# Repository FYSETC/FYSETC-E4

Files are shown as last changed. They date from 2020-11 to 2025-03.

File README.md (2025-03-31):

## Product Introduction

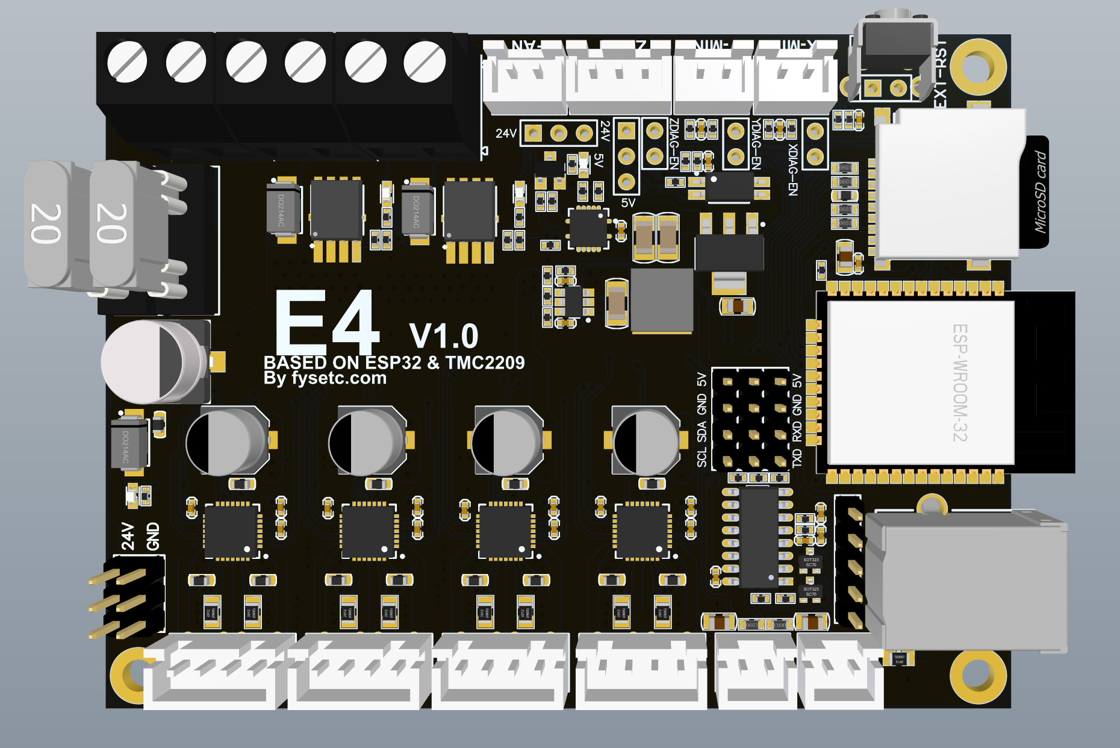
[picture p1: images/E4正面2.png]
E4正面2


The E4 board is a minimal 3D printer control board based on the ESP32 microcontroller from ESPRESSIF, with built-in Wi-Fi and Bluetooth. The controller speed is up to 240MHz, 16M flash.

## Features

- Compact size: 90mm x 67mm
- Native Wi-Fi support
- 12V to 24V input power supply, 3 power outputs and 3 5V outputs
- 4 * **TMC2209** stepper drives: X, Y, Z and E axis
- Onboard TF card socket
- CH340 for high speed USB serial connection 
- X, Y, and Z min endstops; also supports sensorless homing
- Allows the use of a Z-axis probe, such as an inductive sensor, running on the input supply voltage (12V to 24V) or 5V
- A controllable fan, you can choose the power supply voltage (12/24V) or 5V voltage for it
- Xh2.54 connector, firm and easy to plug
- PCB：
  - Black matte ink,lead-free tin spray process
  - High quality, High temperature FR4-TG130 PCB

## Why do you need this board?

If you want to be able to control your 3D printer via a web browser without having to buy extra components like a Raspberry Pi for Octoprint, this board is for you. If you run a printing farm and want to be able to start prints remotely via Wi-Fi, this board is for you. 

### Native Wi-Fi support

FYSETC E4 is based on the ESP32 microcontroller, so the E4 supports 802.11 b/g/n protocols, and a custom fork of Marlin firmware can be used on the board to allow the board to be controlled via a web browser.

This removes the need for the traditional LCD controllers that most other boards use. There is also no need to connect a Raspberry Pi in order to control the printer via a web interface. The web interface is the popular ESP3D webUI, which runs natively on the custom Marlin fork. The printer can then be controlled via any web browser, be it a PC, smart phone, or tablet.

For example, you can slice your 3D model using a slicing software on your PC, then use your PC's web browser to connect to the printer, send the sliced GCODE file to the printer via Wi-Fi. Then, using the same web browser, you can tell the printer to start printing away.

### Trinamic stepper drivers

FYSETC E4 use the latest ,best stepper drvier : TMC2209.

1. Ultra quiet
2. Good heat dissipation
3. Max current up to 2A
4. Large heat sink,good heat dissipation
5. Support sensorless-homing function.

### High voltage for probes

One common problem when using inductive or capactive probes is the voltage which they are powered at. These probes are usually connected to the Z endstop, which is powered directly by the microcontroller. This means 5V or 3.3V, but these probes are not designed for such low voltages. Instead, they are usually designed for operation at 6V or more. Using a lower voltage to operate such probes reduces their detection distance, and therefore their effectiveness.

The FYSETC E4 has a dedicated connector for such a Z probe which uses the voltage of the power supply to power the probe. If you are using 12V for the power supply, the probe will be running on 12V, and vice versa for when using a 24V power supply. This allows the probe to operate within its specifications, delivering optimal detection distances.

### Onboard or External Antenna

There are two versions of the E4 board. One is that the antenna of the WiFi module is onboard. And the other is a WiFi module with an external antenna. This option give you the choice  that if you want to install board in a closed box, the external antenna can avoid the problem of WIFI signal weakening in a confined space.

| Onboard Antenna | External Antenna |
| --- | --- |
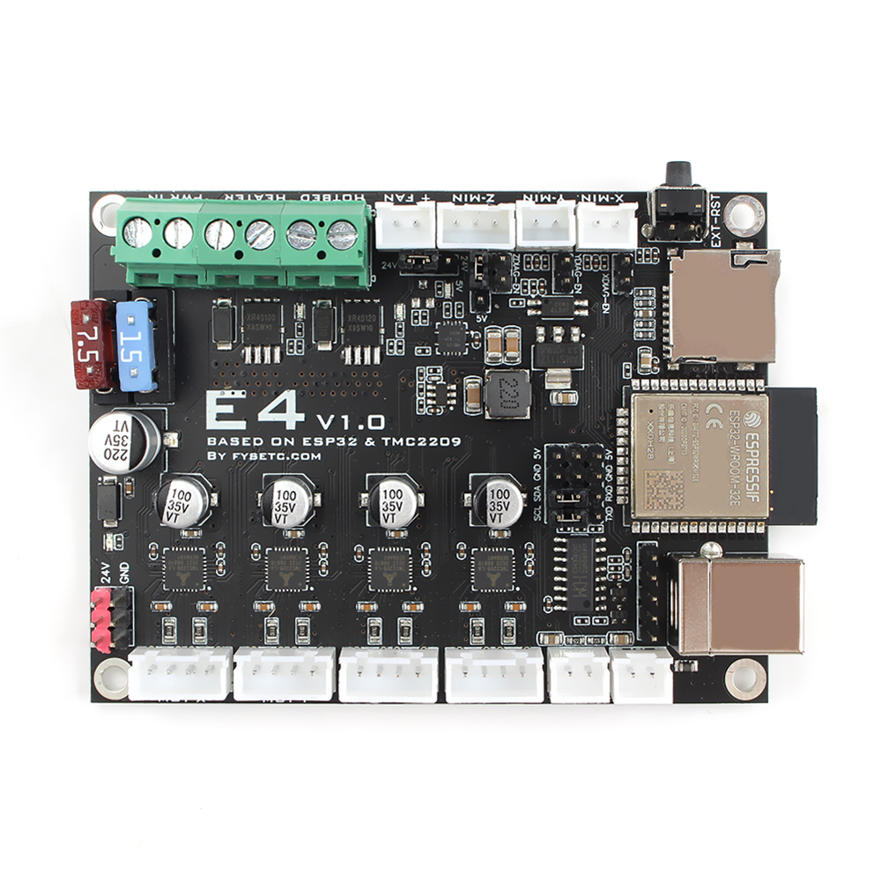
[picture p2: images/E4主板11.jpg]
E4主板11
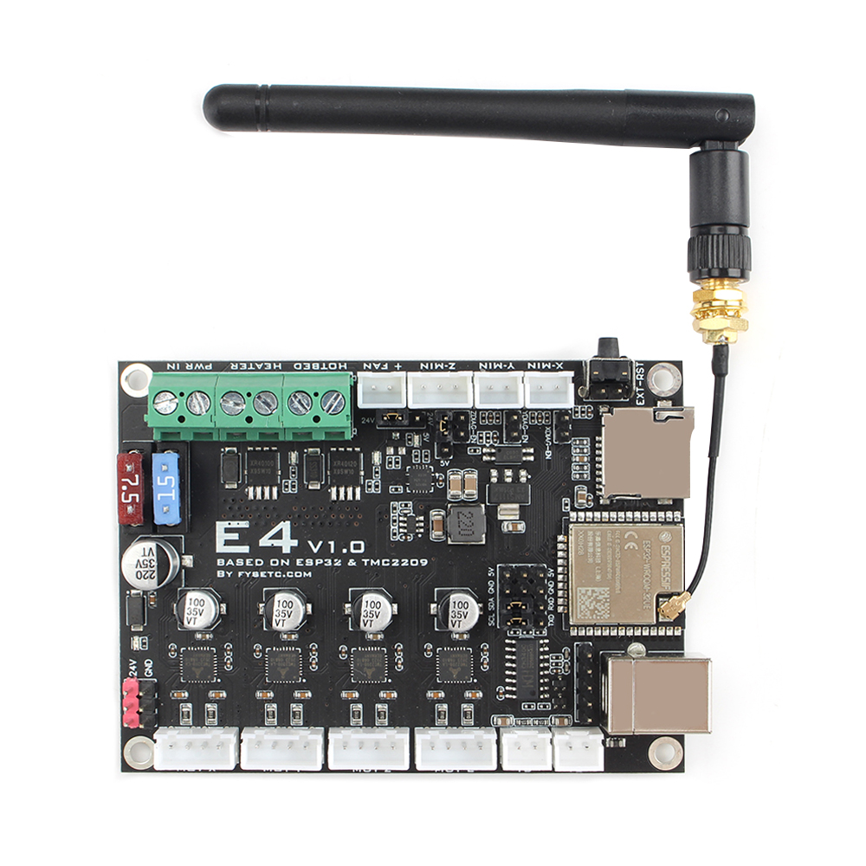
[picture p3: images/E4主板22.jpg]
E4主板22
|  |  |

## Hardware Reasources

E4正面

| Board Name | E4 |
| --- | --- |
| Latest Version | V1.0 |
| Extruders | 1 |
| Hotbed | 1 |
| Controlled Fans  | 1 |
| Heaters | 1 |
| Endstops | 3 |
| Temp sensor | 2 |
| Serial port chip | CH340 |
| CPU | 240MHz [ESP32-WROOM-32E](https://www.espressif.com/sites/default/files/documentation/esp32-wroom-32e_esp32-wroom-32ue_datasheet_en.pdf), [ESP32-WROOM-32UE](https://www.espressif.com/sites/default/files/documentation/esp32-wroom-32e_esp32-wroom-32ue_datasheet_en.pdf) |
| FLASH Size | 16MB |
| Stepper driver | 4 * TMC2209 |
| Input | Main PWR：12-24V 22.5A Max |
| Output | BED+Heater OUT：15A Max |

## Jumper Introduction

**Fan power jumper**

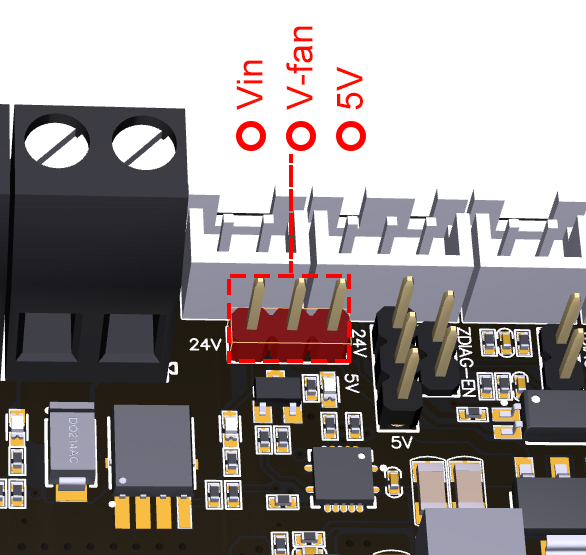
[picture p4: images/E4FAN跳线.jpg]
E4FAN跳线


**Z-Probe power jumper**

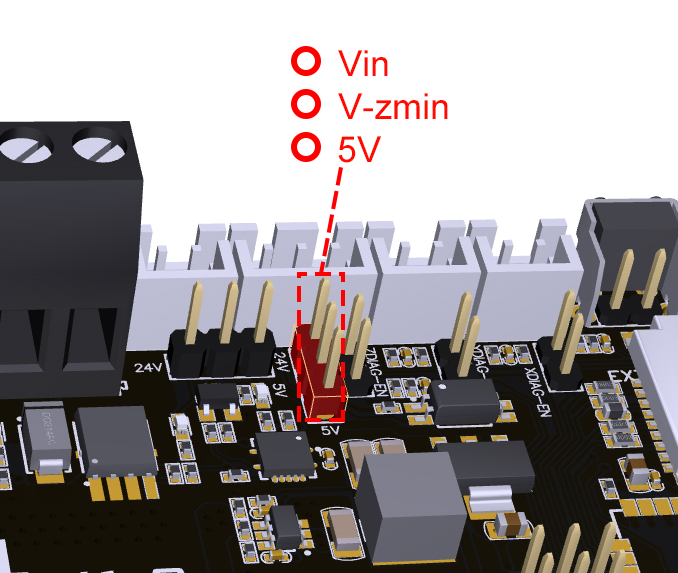
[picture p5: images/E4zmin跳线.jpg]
E4zmin跳线


**Sensorless homing enable jumper**

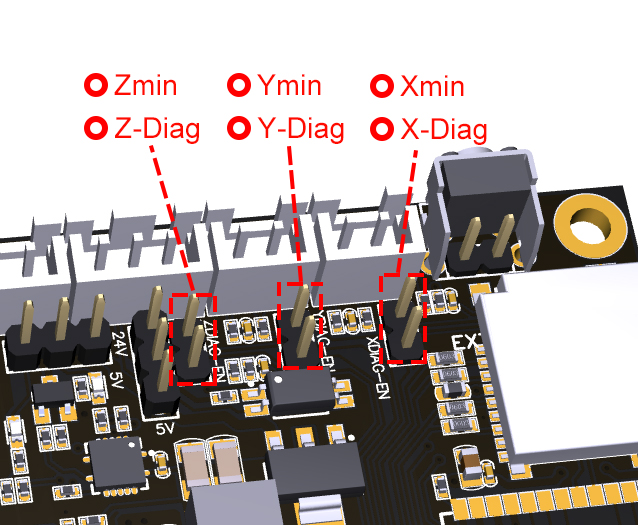
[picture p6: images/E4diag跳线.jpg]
E4diag跳线


**Sensorless homing enable jumper**

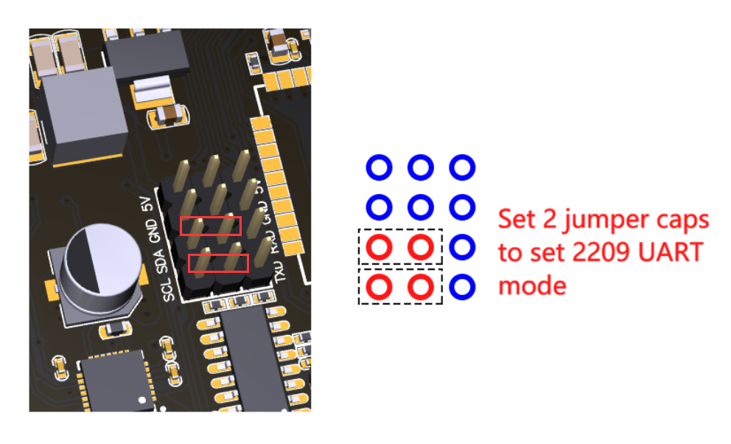
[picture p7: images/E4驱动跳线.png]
E4驱动跳线


## Pin Definition

<table>
   <tr><td>Features</td><td>E4 Pin</td><td>ESP32 Pin</td><td>Pin No.</td><td>Comment</td></tr>
   <tr><td rowspan="3">X-MOTOR(1)</td><td>X-Step</td><td>27</td><td>12</td><td></td></tr>
   <tr><td>X-DIR</td><td>26</td><td>11</td><td></td></tr>
   <tr><td>X-EN</td><td>25</td><td>10</td><td></td></tr>
   <tr><td rowspan="3">Y-MOTOR(2)</td><td>Y-Step</td><td>33</td><td>9</td><td></td></tr>
   <tr><td>Y-DIR</td><td>32</td><td>8</td><td></td></tr>
   <tr><td>Y-EN</td><td>25</td><td>10</td><td></td></tr>
   <tr><td rowspan="3">Z-MOTOR(3)</td><td>Z-Step</td><td>14</td><td>13</td><td></td></tr>
   <tr><td>Z-DIR</td><td>12</td><td>14</td><td></td></tr>
   <tr><td>Z-EN</td><td>25</td><td>10</td><td></td></tr>
   <tr><td rowspan="3">E0-MOTOR(4)</td><td>E0-Step</td><td>16</td><td>27</td><td></td></tr>
   <tr><td>E0-DIR</td><td>17</td><td>28</td><td></td></tr>
   <tr><td>E0-EN</td><td>25</td><td>10</td><td></td></tr>
   <tr><td rowspan="3">SPI </td><td>MOSI</td><td>23</td><td>37</td><td></td></tr>
   <tr><td>MISO</td><td>19</td><td>31</td><td></td></tr>
   <tr><td>SCK</td><td>18</td><td>30</td><td></td></tr>
   <tr><td rowspan="3">End-stops</td><td>X-MIN</td><td>34</td><td>6</td><td>Share with X-DIAG</td></tr>
   <tr><td>Y-MIN</td><td>35</td><td>7</td><td>Share with Y-DIAG</td></tr>
   <tr><td>Z-MIN</td><td>15</td><td>23</td><td>Share with Z-DIAG</td></tr>
   <tr><td rowspan="1">FAN</td><td>FAN0</td><td>13</td><td>16</td><td></td></tr>
   <tr><td rowspan="2">Heating</td><td>E0-Heater</td><td>2</td><td>24</td><td></td></tr>
   <tr><td>Heated-Bed</td><td>4</td><td>26</td><td></td></tr>
   <tr><td rowspan="2">Temperature</td><td>TE0（THERM0）</td><td>36</td><td>4</td><td>A 4.7kOhm 0.1% temperature sensor pull up resistor is used,PT1000 can be connected directly. For PT100, an amplifier board must be used.</td></tr>
   <tr><td>TB</td><td>39</td><td>5</td><td></td></tr>
   <tr><td rowspan="2">MOTOR UART</td><td>TX1</td><td>22</td><td>35</td><td></td></tr>
   <tr><td>RX1</td><td>21</td><td>34</td><td></td></tr>
</table>

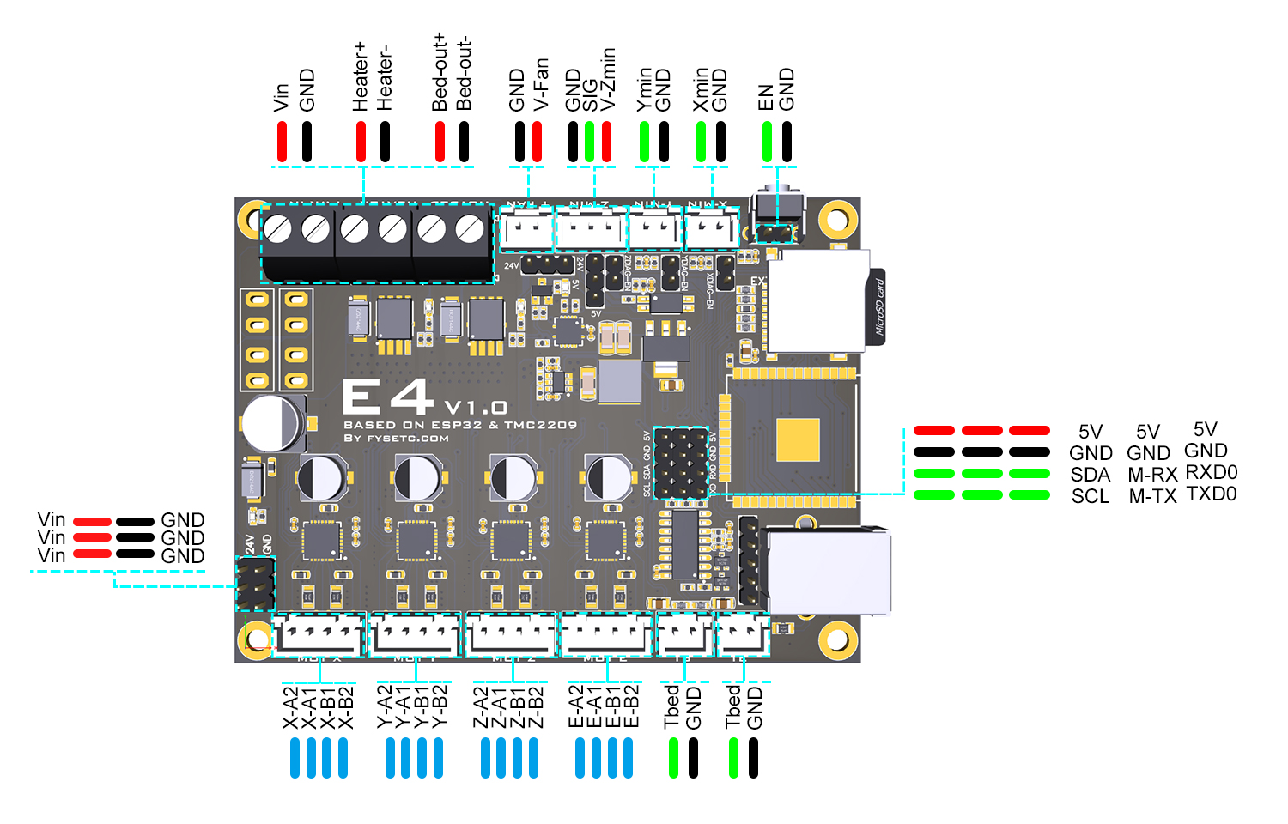
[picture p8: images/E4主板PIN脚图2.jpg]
E4主板PIN脚图2


## Dimensions

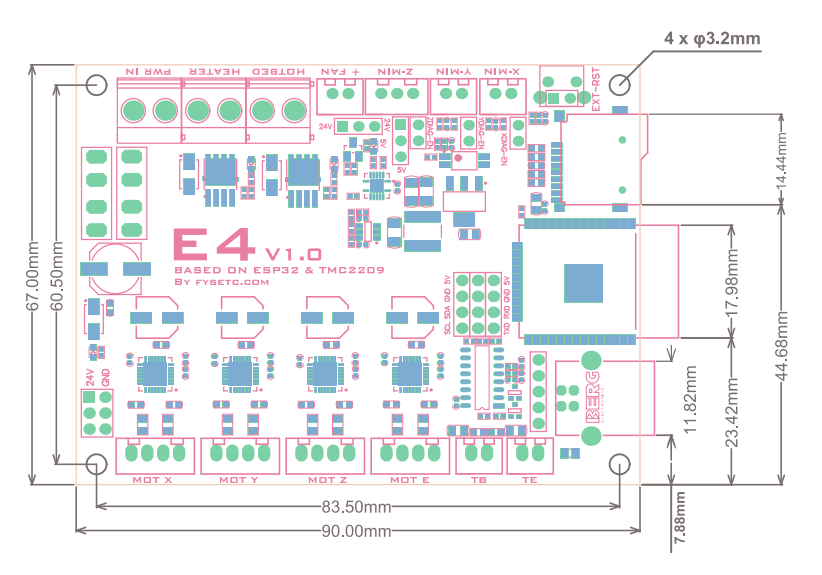
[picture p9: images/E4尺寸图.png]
E4尺寸图


---

- [Schematic and PCB files](https://github.com/FYSETC/FYSETC-E4/tree/main/hardware)

## Firmware

### How to use

The factory firmware comes flashed with the custom fork of Marlin as well as the web interface. You can get it in our [github](https://github.com/FYSETC/FYSETC-E4). Always you need to modify it base on your machine configuration. You can follow our [video](https://youtu.be/Skz7xW8TiHI) or the following steps :

1. Turn on power to the FYSETC E4, and then connect your PC, smart phone, or tablet to the SSID "MARLIN_ESP" (default password is "12345678").
2. Once connected, open a web browser, and go to "[http://192.168.0.1/](http://www.google.com/url?q=http%3A%2F%2F192.168.0.1%2F&sa=D&sntz=1&usg=AFQjCNHmcUXoQvvfhtmwWsGrZOfa2vJB6A)" which will load the ESP3D web interface.
3. Go to the "ESP3D" tab, and enter your WiFi settings (SSID and password).
4. Reset the FYSETC E4. It should now connect to your router.
5. Connect the USB cable to E4 and your PC with 115200 baudrate, and send Serial command "[ESP111]" to get the E4 IP address.
6. Use your web browser and visit the IP address you just get to access the web interface.
7. You can now update the firmware. Download the custom fork from [here](https://github.com/FYSETC/FYSETC-E4/tree/main/firmware), edit Configuration.h and Configuration_adv.h to suit your needs, then compile. In PlatformIO, you can add "upload_port = ip adderrs of your E4" to your platformio.ini file to allow OTA updates. Or, after the firmware has been compiled, use the web interface, go to "ESP3D" tab, and there is an option for firmware update that allows up to upload the firmware.bin file.

### Compile the firmware yourself

If you want to compile the firmware yourself, you need to 

1. Edit the `configuration.h` and `configuration_adv.h` file , please follow the README [here](https://github.com/luc-github/ESP3DLib).

2. Change env in `platformio.ini` to `FYSETC_E4`
   
   ```default_envs = FYSETC_E4```

#### Marlin 2.1.x

Get the code from Marlin github [here](https://github.com/MarlinFirmware/Marlin), and the related configuration [here](https://github.com/luc-github/MarlinConfigurations/tree/bugfix-2.1.x/config/examples/FYSETC/E4).

## Shop

---

- [Taobao](https://item.taobao.com/item.htm?spm=a230r.1.14.22.66cd74cfpASnTX&id=641701271442&ns=1&abbucket=1#detail)
- [Aliexpress](https://www.aliexpress.com/item/1005001703930983.html)

## Tech Support

---

Please submit any technical issue into our [github](https://github.com/FYSETC/FYSETC-E4) or [forum](http://forum.fysetc.com/)

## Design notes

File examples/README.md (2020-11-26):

# Examples

This folder will contains machine examples that E4 board supporting. If you can't find your printer here , it does not mean E4 board does not support it , just because we don't add it at the moment. We strongly encourage you to make PR  for us and here is the [tutorial](https://docs.github.com/en/free-pro-team@latest/github/collaborating-with-issues-and-pull-requests/creating-a-pull-request). Thanks for your support.

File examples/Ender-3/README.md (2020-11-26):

# Ender3

This  setup up guide is for installing FYSETC E4 to Ender3  machine.

## Structure

You need to print two files with your 3D printer first named ```Case.STL``` and ```Cover.STL```. Then uninstall the original Ender 3 case and cover, then install these two printing part to Ender3.  

## Firmware

Replace Marlin with ```configuration.h``` and  ```configuration_adv.h``` beside this README  file. Then compile and upload.

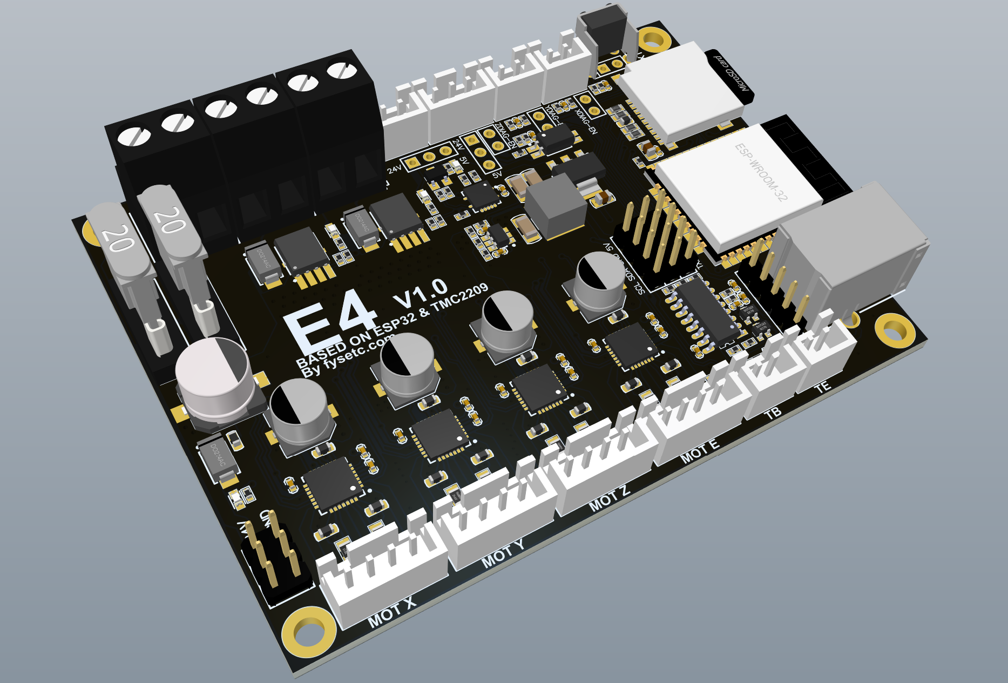
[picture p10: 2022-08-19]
hardware/E4_3Dview.png

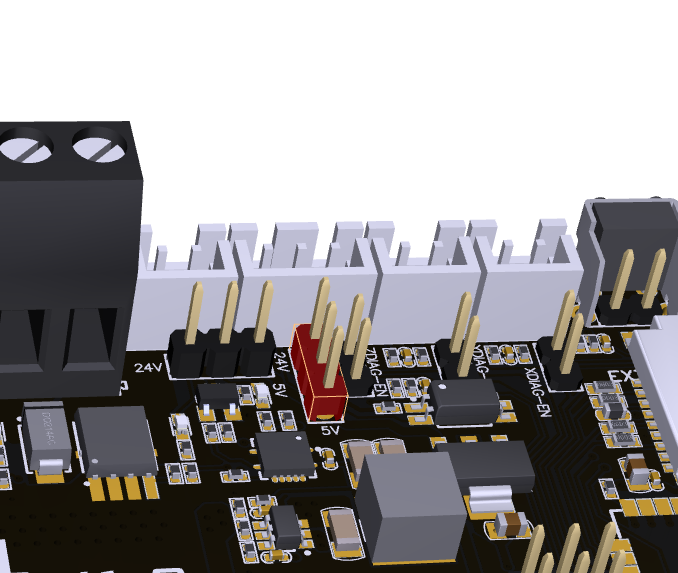
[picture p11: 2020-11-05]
images/E4zmin跳线.png

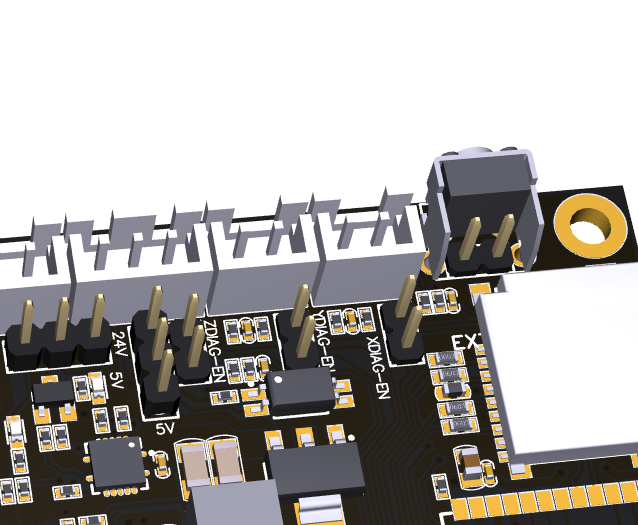
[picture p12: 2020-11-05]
images/E4diag跳线.png

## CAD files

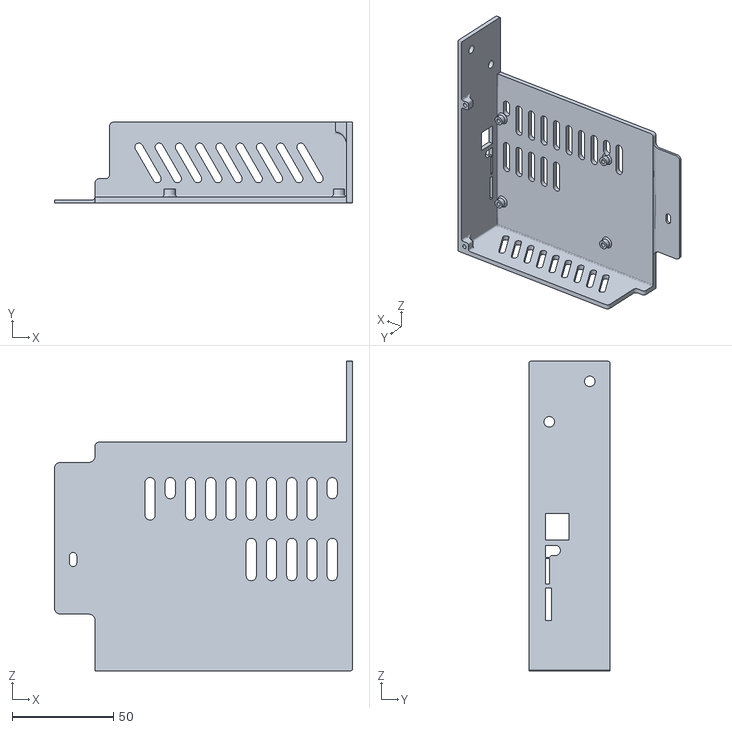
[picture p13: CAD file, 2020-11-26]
examples/Ender-3/Case.STL
147.2 x 40.0 x 153.0

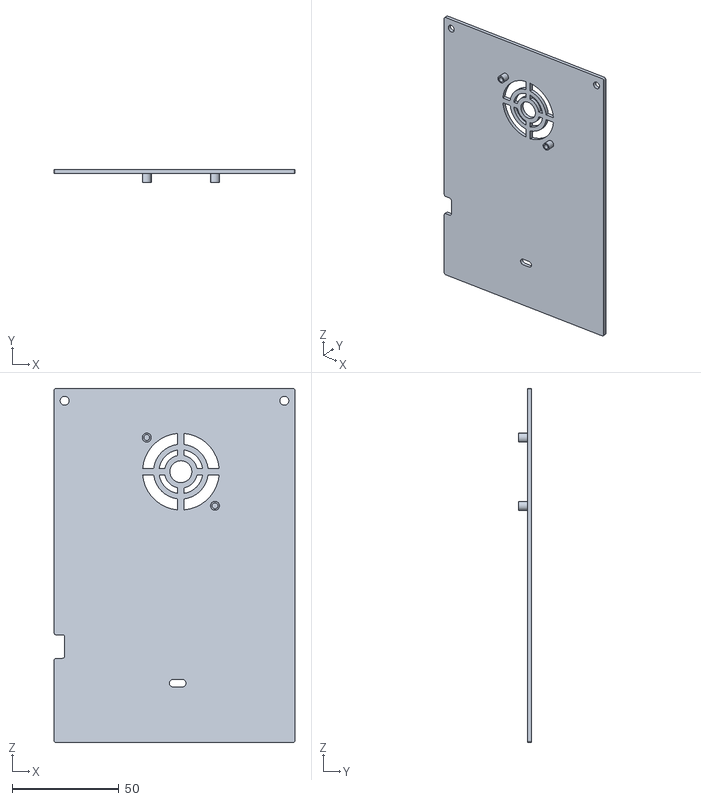
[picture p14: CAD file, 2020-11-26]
examples/Ender-3/Cover.STL
113.0 x 6.20 x 166.0

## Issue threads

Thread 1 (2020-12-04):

FYSETC-E4 Setup Example For a Delta Printer

Loadmaster1, 2020-12-04:
The provided E4 is for a cartesian printer.  Is there a chance of a working example for a Delta type of printer?  I have a Tevo Little Monster that I am trying to use the E4 with.  I keep having issues with the build failing.  Something to do with the Pins.

I will continue to try and resolve the build error, but any input would be much appreciated.

GerogeFu, 2020-12-04:
Sorry , this board only have 3 endstops pin. And there is no enough pin for a servo or bltouch.  But i have a thought , if you don't have a heatbed , maybe you can use the heatbed pin PC9 for bltouch. That means , you need to change pins_FYSETC_E4.h file as below.

Loadmaster1, 2020-12-04:
Geroge,  thank you for your suggestion.  I will give it a go and see if I can figure this out.

Loadmaster1, 2020-12-04:
Geroge, I really like the design and wifii of the E4 board.  Does FYSETC have any plans to build a board like the E4 with added endstops for use with a Delta design?  I believe there is a huge market for such.  It would be worth considering.

GerogeFu, 2020-12-05:
Yes , we are planning now. Hope more and more people like E4 boards. And it is nealy support Grbl_ESP32 firmware now. https://github.com/bdring/Grbl_Esp32

Loadmaster1, 2020-12-05:
That is great news.  You guys did a nice job on the E4.  Yes, I'm sure there will be a lot of interest.

________________________________
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

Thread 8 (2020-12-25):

Fan always on

sdavidozzo, 2020-12-25:
I installed the firmware found here on my ender 3 but the fan is always on.
Sending the M106 S0 command or the M107 command gives me a message:
Ok
ok
but the fan remains on as well as the LED on the board.

GerogeFu, 2021-01-06:
Can you take a pic for me? It is a bit hard to tell from what you describe.

sdavidozzo, 2021-01-13:
[image: E4.jpg]
When I turn on the printer, the fan for cooling the filament turns on as
well as the red LED. When printing begins, the fan stays on and in this way
the piece does not stick to the plate. It never goes out even when sending
the M106 S0 command

Il giorno mer 6 gen 2021 alle ore 09:16 George Fu <notifications@github.com>
ha scritto:

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

GerogeFu, 2021-01-27:
Are you using stock firmware ? Or you compile the firmware yourself ?

sdavidozzo, 2021-01-27:
I tried both with stock firmware and compiled firmware but can’t solve the problem

Inviato da iPad

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

GerogeFu, 2021-02-02:
Do you have a multimeter? You can measure the vol of mosfet pin1 , if the voltage changes if you send commands(M106) to turn it on then off. Then the mosfet is dead. If the voltage of pin1 not change, that is the firmware or other issue not mosfet.
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

sdavidozzo, 2021-02-02:
The volt of mosfet pin1 change from 0 (M106 S0) to 1,84 volt (M106 S200) . The mosfet is dead?

GerogeFu, 2021-02-03:
Can you measure this pin vol for me ?
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

GerogeFu, 2021-02-04:
No matter how, contact our sales to send you another E4 board for you.

iNDeX999, 2021-08-06:
I had the same problem, Mosfet dead, new board is on it's way.

sdavidozzo, 2021-08-07:
I had to reinstall the original card and am still waiting for the replacement. I have lost all hope of seeing this card working by now.

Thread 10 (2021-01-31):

Config marlin

smashemQuads, 2021-01-31:
Need help custom config marlin. Vs code platform io.
Librays dont install
Bugfix doesnt have e4 board.
Where do i get a working version i can edit please

GerogeFu, 2021-02-01:
The lastest  bugfix2.0 has E4
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

smashemQuads, 2021-02-20:
Fixed, Issue is with VS code not getting libaries.

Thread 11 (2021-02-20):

PIN Numbers please

smashemQuads, 2021-02-20:
Can I get the Pin numbers for RXD0 and TXD0
Are they allocated to anything?
Thanks

Tigger777, 2021-04-21:
The schematic is in this repo, those pins are used for USB Serial comms.

iNDeX999, 2021-08-06:
The ESP32 has 3 uart:

<html>
<body>
<!--StartFragment-->

UART0 | GPIO3 | GPIO1 | N/A | N/A
-- | -- | -- | -- | --
UART1 | GPIO9 | GPIO10 | GPIO6 | GPIO11
UART2 | GPIO16 | GPIO17 | GPIO8 | GPIO7

<!--EndFragment-->
</body>
</html>

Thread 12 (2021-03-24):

Servo Usage, which pin is accessible?

theomega, 2021-03-24:
I want to use a servo instead of the Z-Axis Stepper motor. The servo would be PWM controlled which is something the ESP32 firmware can support on every GPIO pin.

Is there any GPIO pin from the ESP32 accessible on the board that can be used for this?

Tigger777, 2021-04-21:
I used GPIO0 for a Z-probe ABL servo. You need to solder a wire to the ESP32 (bottom pin on the RHS). You also need a pull-up to 3v3 else it won't always boot.  I had already installed everything so I just tied to to 5V with a 39k resistor.

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

lols, 2021-06-16:
you can use the z-min plug for servo but you need to see the board pcb
-remove the opto isolator + filter cap + 3.3v pull up resistor(red box)
-bridge the opto isolator pin(green line)
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

car-par, 2024-10-20:
Hi, I'm new to this and I would like to use a BLTouch on a Fysetc E4 but idk where to connect the PWM cable... and I didn't really understand what you all said in the comments above... Please could someone help me?

Tigger777, 2024-10-21:
> Hi, I'm new to this and I would like to use a BLTouch on a Fysetc E4 but idk where to connect the PWM cable... and I didn't really understand what you all said in the comments above... Please could someone help me?

Look above at my screenshot, the orange arrow is pointing to GPIO0, thats where to connect the PWM signal.
Can you build the Marlin code? This has been quite an undertaking for me every time there have been updates.

car-par, 2024-10-28:
Hi, sorry if I'm replying after a week, I didn't see you had replied. Ok I understood that I had to connect the PWM to GPIO0 but as for the rest it's not clear to me how to proceed. And yes I can build the code. Thanks for your reply

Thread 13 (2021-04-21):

Print pauses and leaves blobs

Tigger777, 2021-04-21:
I've experienced some issues which I think are related to web access.  I've not looked how the websockets have been implemented but I trust the people who wrote the code are better programmer than me.

It appears to happen when my PC goes to sleep (iMac) with safari open on the ESP3D page.

I make a point of closing the browser tab every time as a work around, and I've only seen it once leave a blob in a 12 hour print.

I replaced a random layer shifting board in a Ender 3 V2 with this one and I am very pleased with the results.  The vertical walls are so much cleaner/smoother.

Also the machine uses less power now, the PSU fan turns off during a print and the hottest stepper motor is now 38 degC, I couldn't touch them on the stock setup.

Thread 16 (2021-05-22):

How to connect a bltouch without heatbed?

lols, 2021-05-22:
How can I connect all the pins to a bltouch?
I can solder/cut trace etc just don't know which pin to use and config

KittyDotNet, 2022-09-16:
change your homing to
```
//#define QUICK_HOME
#define HOME_Y_BEFORE_X
```
to fix the end stop issue

Closed 2021-06-16.

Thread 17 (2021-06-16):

Fix the bottom silkscreen

lols, 2021-06-16:
The bottom silkscreen is different from the top silkscreen for all the stepper connector

earlynerd, 2022-03-24:
I have made a pull request which addresses this issue, as well as including a more complete 3D model. It even includes the mounting holes.

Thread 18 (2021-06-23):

Klipper Support for E4 boar

IXMAN89, 2021-06-23:
Hi,

Ist planed to support Klipper Firmware with the E4 board and ESP32 chip.
Is somebody working on that?
Also is it planned to have web interface Mainsail run on the board as well without using an Raspberry pi.

Greetings Ixman

cranefist, 2022-09-22:
You should ask Klipper people to support ESP32, for some reason they don't support it even though its superior to any other MCU.

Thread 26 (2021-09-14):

Feature request for E4 V1.1

walemke, 2021-09-14:
I have just started using the E4 and I am impressed with the simple KISS approach. It just works. But I have two feature request for a E4 V1.1 board. The first is a Bed level sensor. I would like to uses this with a delta printer. The second request is for a interface to one of the cheap OLED displays for ESP that can show hot end temp, bed temp and print progress. The URL works but would be nice to have a OLED on the printer so when I look at it I can see where the print is at.

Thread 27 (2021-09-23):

No Wi-Fi after Marlin update

Vassssko, 2021-09-23:
Hello.

I can not figure out how to connect to the board anymore: I have successfully complied and flashed Marlin 2.0.9.1 for the E4 board (using ESP web interface, as I was able to connect the board to home wifi network). After that E4 disappears from my wifi network, but it successfully works with USB connection and repetier host - it communicates just well.

Could you please share how to got wi-fi working back? There is no marlin esp device in wi-fi network as well.

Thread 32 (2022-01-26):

default password

xrenznaet, 2022-01-26:
MARLIN_ESP sees the access point, but does not accept the default password. how to solve the problem?

Closed 2022-01-27.

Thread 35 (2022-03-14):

E4 Web interface: How to show bed temperature?

Reefeiro, 2022-03-14:
E4 is showing T0 as a target to both hotend AND bed temperature. Is there any way so the system returns te Hotend AND te bed temperature, not only hotend?
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

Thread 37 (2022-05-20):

SD Card Not Detecting

lancesand, 2022-05-20:
Hello, I recently received one of these boards but I'm having trouble using the SD card on it.  It does not seem to be detecting an SD card present in the slot. Has anyone else dealt with this error?

marcioscardua, 2022-09-12:
I have same problem

NellClarke, 2023-06-27:
Has this problem been solved?
I can't find any solution for it, and FYSETC doesn't seem to update the code at all anymore.

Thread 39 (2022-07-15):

Does anyone have schematic of board ?

12520349, 2022-07-15:
I want to reprogram for my private purpose! Please give me schematic , Thank you

12520349, 2022-07-18:
I found. thank you!

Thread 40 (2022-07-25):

Failed to build firmware on latest PlatformIO

25879, 2022-07-25:
I failed to build the firmware downloaded from here after i upgrad PlatformIO to the latest version (Core 6.1.3).
It seems that the build-in library of ESP32 cannot be read correctly.
Please help...
Part of the log attached below..
```
Found 38 compatible libraries
Scanning dependencies...
Dependency Graph
|-- TMCStepper @ 0.7.3
|   |-- SPI @ 1.0
|-- Adafruit MAX31865 library @ 1.1.0
|   |-- SPI @ 1.0
|-- Adafruit NeoPixel @ 1.5.0
|-- U8glib-HAL @ 0.4.1
|   |-- Wire @ 1.0.1
|   |-- SPI @ 1.0
|-- Arduino-L6470 @ 0.8.0
|-- SlowSoftI2CMaster @ 1.0.0
|-- AsyncTCP @ 1.1.1
|-- ESP Async WebServer @ 1.2.3
|   |-- AsyncTCP @ 1.1.1
|   |-- FS @ 1.0
|   |-- WiFi @ 1.0
|-- ESP3DLib @ 1.0.11+sha.5a2d484
|   |-- FS @ 1.0
|   |-- SPIFFS @ 1.0
|   |   |-- FS @ 1.0
|   |-- WiFi @ 1.0
|   |-- U8glib-HAL @ 0.4.1
|   |   |-- Wire @ 1.0.1
|   |   |-- SPI @ 1.0
|   |-- WebSockets @ 2.3.7+sha.dd8675c
|   |   |-- WiFi @ 1.0
|   |   |-- SPI @ 1.0
|   |-- ESP32SSDP @ 1.2.0+sha.6d78df5
|   |   |-- WiFi @ 1.0
|   |-- ESPmDNS @ 1.0
|   |   |-- WiFi @ 1.0
|   |-- Update @ 1.0
|   |-- ArduinoOTA @ 1.0
|   |   |-- Update @ 1.0
|   |   |-- WiFi @ 1.0
|   |   |-- ESPmDNS @ 1.0
|   |   |   |-- WiFi @ 1.0
|-- WebSockets @ 2.3.7+sha.dd8675c
|   |-- WiFi @ 1.0
|   |-- SPI @ 1.0
|-- ESP32SSDP @ 1.2.0+sha.6d78df5
|   |-- WiFi @ 1.0
|-- SPI @ 1.0
|-- EEPROM @ 1.0.3
|-- ArduinoOTA @ 1.0
|   |-- Update @ 1.0
|   |-- WiFi @ 1.0
|   |-- ESPmDNS @ 1.0
|   |   |-- WiFi @ 1.0
|-- ESPmDNS @ 1.0
|   |-- WiFi @ 1.0
|-- WiFi @ 1.0
|-- FS @ 1.0
|-- SPIFFS @ 1.0
|   |-- FS @ 1.0
|-- Wire @ 1.0.1
Building in release mode
Warning! We have just detected `upload_port` as IP address or host name of ESP device. `upload_protocol` is switched to `espota`.
Please specify `upload_protocol = espota` in `platformio.ini` project configuration file.
Compiling .pio\build\fysetc_e4\src\src\HAL\ESP32\FlushableHardwareSerial.cpp.o

... skip...

Compiling .pio\build\fysetc_e4\lib26e\arduinoWebSockets\WebSocketsClient.cpp.o
Compiling .pio\build\fysetc_e4\lib26e\arduinoWebSockets\WebSocketsServer.cpp.o
Compiling .pio\build\fysetc_e4\lib26e\arduinoWebSockets\libb64\cdecode.c.o
Compiling .pio\build\fysetc_e4\lib26e\arduinoWebSockets\libb64\cencode.c.o
Archiving .pio\build\fysetc_e4\lib148\libESPAsyncWebServer.a
In file included from .pio\libdeps\fysetc_e4\arduinoWebSockets\src\SocketIOclient.cpp:8:0:
.pio\libdeps\fysetc_e4\arduinoWebSockets\src\WebSockets.h:190:30: fatal error: WiFiClientSecure.h: No such file or directory

**************************************************************************
* Looking for WiFiClientSecure.h dependency? Check our library registry!
*
* CLI  > platformio lib search "header:WiFiClientSecure.h"
* Web  > https://registry.platformio.org/search?q=header:WiFiClientSecure.h
*
**************************************************************************

compilation terminated.
*** [.pio\build\fysetc_e4\lib26e\arduinoWebSockets\SocketIOclient.cpp.o] Error 1
In file included from .pio\libdeps\fysetc_e4\arduinoWebSockets\src\WebSockets.cpp:25:0:
.pio\libdeps\fysetc_e4\arduinoWebSockets\src\WebSockets.h:190:30: fatal error: WiFiClientSecure.h: No such file or directory

**************************************************************************
* Looking for WiFiClientSecure.h dependency? Check our library registry!
*
* CLI  > platformio lib search "header:WiFiClientSecure.h"
* Web  > https://registry.platformio.org/search?q=header:WiFiClientSecure.h
*
**************************************************************************

compilation terminated.
*** [.pio\build\fysetc_e4\lib26e\arduinoWebSockets\WebSockets.cpp.o] Error 1
In file included from .pio\libdeps\fysetc_e4\arduinoWebSockets\src\WebSocketsClient.cpp:25:0:
.pio\libdeps\fysetc_e4\arduinoWebSockets\src\WebSockets.h:190:30: fatal error: WiFiClientSecure.h: No such file or directory

**************************************************************************
* Looking for WiFiClientSecure.h dependency? Check our library registry!
*
* CLI  > platformio lib search "header:WiFiClientSecure.h"
* Web  > https://registry.platformio.org/search?q=header:WiFiClientSecure.h
*
**************************************************************************

compilation terminated.
*** [.pio\build\fysetc_e4\lib26e\arduinoWebSockets\WebSocketsClient.cpp.o] Error 1
In file included from .pio\libdeps\fysetc_e4\arduinoWebSockets\src\WebSocketsServer.cpp:25:0:
.pio\libdeps\fysetc_e4\arduinoWebSockets\src\WebSockets.h:190:30: fatal error: WiFiClientSecure.h: No such file or directory

**************************************************************************
* Looking for WiFiClientSecure.h dependency? Check our library registry!
*
* CLI  > platformio lib search "header:WiFiClientSecure.h"
* Web  > https://registry.platformio.org/search?q=header:WiFiClientSecure.h
*
**************************************************************************

compilation terminated.
*** [.pio\build\fysetc_e4\lib26e\arduinoWebSockets\WebSocketsServer.cpp.o] Error 1
======================================================================================== [FAILED] Took 447.78 seconds ========================================================================================

Environment    Status    Duration
-------------  --------  ------------
fysetc_e4      FAILED    00:07:27.785
==================================================================================== 1 failed, 0 succeeded in 00:07:27.785 ===================================================
=================================
```

brunoeiti, 2022-08-10:
Same problem here,  looking for a solution

cineast1, 2022-08-13:
Exactly same problem here, too

GerogeFu, 2022-08-19:
The firmware on the repo is pretty old one, seems have compatibility with latest platformio, anyone try latest marlin?

craftbot, 2022-08-20:
platformio is latest firmare from this github

craftbot, 2022-08-27:
Ie you need You need the following in Configuration_adv.h

  #define  X_SLAVE_ADDRESS 0
  #define  Y_SLAVE_ADDRESS 2
  #define  Z_SLAVE_ADDRESS 1
  #define E0_SLAVE_ADDRESS 3

in platformio.ini
[platformio]
src_dir      = Marlin
boards_dir   = buildroot/share/PlatformIO/boards
default_envs = fysetc_e4
include_dir  = Marlin

need config for your printer Configuration.h

Tigger777, 2022-09-14:
> The firmware on the repo is pretty old one, seems have compatibility with latest platformio, anyone try latest marlin?

I've got the latest Marlin 2.1.x to build and work as before.  It's not really that difficult if you follow Luc's instructions.

I used the default config files and modded them as follows:-

Configuration.h
============
1. Motherboard : BOARD_FYSETC_E4 2.
2. #define SERIAL_PORT_2 -13.
3. Change steppers drivers to TMC2209
4.Set Temp sensor 1 & bed to thermistor 1
5. Invert Stepper Directions to suit your setup.
6. Enable SDSUPPORT

Configuration_adv.h
===============
1. Uncomment  #define BABYSTEP_ZPROBE_OFFSET          // Combine M851 Z and Babystepping
2. Change sense resistor values from 0.11 to 0.22 - These were set to 0.11 in the fysetc repo here I'm not sure why - GeorgeFu do you know why?
3. Set the slave addresses of the TMS drivers as per craftbot's post above.

PlatformIO.ini
==========
as per the above craftbot's post

I have also implemented a BL/CR touch on GPIO 0, but this requires a few more files to be changed.

4kardes, 2022-10-14:
same problem cant find solution

4kardes, 2022-10-16:
how about for 2.0.9
platform = espressif32@3.4
not working (compile but size too low and not work)
#define SERIAL_PORT_2 -1  getting error

Tigger777, 2022-10-17:
Sorry mate, that version doesn't compile anymore on my machine. Most probably from incessant updates to VSCode/Platform IO, you'd think they'd dial it back a bit now that they're supposed to be at war and all.  Try building 209 with ***@***.***, but you get wificlientsecure.h and a host of other errors each time you forcibly copy the files it's looking for into the project.  On Oct 16, 2022, at 8:30 PM, 4kardes ***@***.***> wrote:how about for 2.0.9 Some Drawings not working (compile but size too low and not work) #define SERIAL_PORT_2 -1  getting error—Reply to this email directly, view it on GitHub, or unsubscribe.You are receiving this because you commented.Message ID: ***@***.***>

Juaneeto89, 2024-12-21:
Hello! I might be a little late to the party but I just got this same problem and found a way to solve it!

Basically, the problem is that  the board does not exist in PlatformIO. So what I did is I took another ESP32 based board like MKS TINYBEE, downloaded its firmware and started modifying the board file (json file in the board directory) to refer to the same pins that Fysetc E4 uses, I modified all the parameters to make it work on the same pinout and modified the configuration.h and configuration_adv.h according to what was refered in this thread. In other words, i preformed surgery on the firmware to make it believe it was being installed on a mks tinybee.

it worked. Let's hope you guys can get it to work, too.

suliaman99, 2025-05-17:
@Juaneeto89
That is great, can you send your firmware file

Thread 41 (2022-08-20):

How To Correctly Set The Motor Current Limit on board?

12520349, 2022-08-20:
Anyone know? please help me, thank you so much!

cranefist, 2022-09-22:
Via UART

12520349, 2022-10-14:
Sorry, i'm a newbie! Can you give me more information about that? Thank you so much :)

Tigger777, 2022-10-14:
From the code terminal in the web interface (or via usb with pronterface) issue a M906 command to set one or more stepper currents.

M906 X550 Y550 Z650

Sets x & y to 550mA and z to 650mA.

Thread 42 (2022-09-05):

Fix for WiFiClient library compilation fails again!

umartechboy, 2022-09-05:
Looks like it is supposed to have already been addresses in "Update platformio.ini to fix class WiFiClientSecure compilation error" {4b360345fc22ea1cb86909525ceb3c459a040e4e}, but for me it's still failing. Can't build the firmware!

Build terminal output:
...
...
Compiling .pio\build\fysetc_e4\lib53d\arduinoWebSockets\WebSocketsClient.cpp.o
Compiling .pio\build\fysetc_e4\lib53d\arduinoWebSockets\WebSocketsServer.cpp.o
In file included from .pio/libdeps/fysetc_e4/arduinoWebSockets/src/WebSockets.cpp:25:0:
.pio/libdeps/fysetc_e4/arduinoWebSockets/src/WebSockets.h:192:30: fatal error: WiFiClientSecure.h: No such file or directory

craftbot, 2022-09-24:
need use marlin latest version

4kardes, 2022-10-07:
also not compile with new marlin 2.1.1

craftbot, 2024-02-03:
there should be no spaces on the path to the Marlin firmware

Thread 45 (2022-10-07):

can't compile with new Platformio

4kardes, 2022-10-07:
cant compile with new platformio

getting error

Compiling .pio\build\fysetc_e4\liba94\arduinoWebSockets\WebSockets.cpp.o
In file included from .pio\libdeps\fysetc_e4\arduinoWebSockets\src\SocketIOclient.cpp:8:0:
.pio\libdeps\fysetc_e4\arduinoWebSockets\src\WebSockets.h:190:30: fatal error: WiFiClientSecure.h: No such file or directory

**************************************************************************
* Looking for WiFiClientSecure.h dependency? Check our library registry!
*
* CLI  > platformio lib search "header:WiFiClientSecure.h"
* Web  > https://registry.platformio.org/search?q=header:WiFiClientSecure.h
*
**************************************************************************

compilation terminated.
In file included from .pio\libdeps\fysetc_e4\arduinoWebSockets\src\WebSockets.cpp:25:0:
.pio\libdeps\fysetc_e4\arduinoWebSockets\src\WebSockets.h:190:30: fatal error: WiFiClientSecure.h: No such file or directory

**************************************************************************
* Looking for WiFiClientSecure.h dependency? Check our library registry!
*
* CLI  > platformio lib search "header:WiFiClientSecure.h"
* Web  > https://registry.platformio.org/search?q=header:WiFiClientSecure.h
*
**************************************************************************

compilation terminated.
*** [.pio\build\fysetc_e4\liba94\arduinoWebSockets\SocketIOclient.cpp.o] Error 1
*** [.pio\build\fysetc_e4\liba94\arduinoWebSockets\WebSockets.cpp.o] Error 1

Tigger777, 2022-10-14:
Have a look at Issue #40 the steps to follow are detailed there. Start with unmodified Marlin 2.1.x source, replace the  attached config files.

You'll need to edit /ini/esp32.ini
edit the first line:-  platform = espressif32@3.4

[Configurations.zip](https://github.com/FYSETC/FYSETC-E4/files/9790220/Configurations.zip)

In the attached files I've added a comments "// !!!DO1409" wherever I made changes.

Good luck

4kardes, 2022-10-15:
thank you very much bro.
I solved the case because of you

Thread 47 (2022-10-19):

Update firmware.

supernacheitor, 2022-10-19:
Recently bought a new FYSETC E4 board, plugging it in doesn't create any wifi so I can update the firmware. Also I don't know how you can put the ESP32 in download mode to upload a new firmware. How can a new firmware be uploaded?

Thanks.

GerogeFu, 2022-11-04:
If you build the firmware yourself, just click the upload button(arrow) on platformio
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

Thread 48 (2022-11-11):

Use TB for Filament Runout.

supernacheitor, 2022-11-11:
I'm using the TB pin for using a endstop for filament runout. The filament sensor runs perfectly but the TE pin don't read the extrusor temperature when I plug the endstop in TB. Can't I use this pin for a filament runout sensor?  Otherwise, is there any other pin on the board that I can use?

Thanks.

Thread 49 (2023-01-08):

Wrong Rsense value on the schematic

kdomanski, 2023-01-08:
The [PDF schematic in this repo](https://github.com/FYSETC/FYSETC-E4/blob/7d8b968673b268ca04cc75f2a27f40a669238c3f/hardware/FYSETC%20E4_V1.0%20SCH.pdf) specifies the drivers' current sense resistors as 0.22R. However, the actual board I received has 0.11R resistors, which are the typical value used for these drivers.

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

ico621, 2024-02-21:
Same here, I was looking everywhere for the 0.22R resistors (I have also 0.11R instead) on the board and I think it's probably a mistake in the pdf schematic.

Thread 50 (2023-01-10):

How to unbrick board after failed firmware update?

mherfurt, 2023-01-10:
In the process of compiling the Marlin firmware with CoreXY support, I flashed the board via its web interface. Strangely, the board now connects to the WiFi network that I had configured before I flashed the board. Unfortunately, the IP address of the board does not expose any service that I can connect to - it seems to be bricked.

Is there a way to flash this board via USB in order to unbrick it?

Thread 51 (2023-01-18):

Download mode not active

leviner18, 2023-01-18:
Hi,
Im trying to upload a sketch from Arduino IDE and i get following error:
A fatal error occurred: Failed to connect to ESP32: Wrong boot mode detected (0x13)! The chip needs to be in download mode.

Is there a possibility to put the board in download mode?

Thank you on advance

Br

apalazzi, 2023-04-01:
I have the same issue, did you find a way to solve it?

Jimbob-B, 2023-06-05:
Seems this can be fixed by adding a capacitor to the reset circuit - see the USB section on this page,

https://onstep.groups.io/g/main/wiki/32747

There's also a bit of a discussion here about similar issues and possible solutions,

https://github.com/espressif/esptool/issues/741

craftbot, 2024-02-03:
connect pin 25 on grnd

Rishi-00, 2024-07-13:
hey i tried this method in ESP-32-WROOM-S model but still thee issue persists, the code is not being upload
Please, help me as i am unable to get a solution
Thanks in advance

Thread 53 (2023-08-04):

Support to LCD module?

RaulTrombin, 2023-08-04:

OriginaldCrypt, 2023-12-30:
The only feature to be the perfect board

TextileTopher, 2023-12-30:
> The only missing feature to be the perfect board

Agreed entirely. This was a really well designed and documented board. :-) There are just a few features I wish it had (a second UART or screen).

I hope they do another revision of the board. I  B would even be willing to make some tutorials for it to help them out.

OriginaldCrypt, 2023-12-30:
> Agreed entirely. This was a really well designed and documented board. :-) There are just a few features I wish it had (a second UART or screen).

Does this mean that there is only one UART to control the TMC, and not available for a display? (having either the display or the TMC software control, not both at the same time)

TextileTopher, 2023-12-30:
> > Agreed entirely. This was a really well designed and documented board. :-) There are just a few features I wish it had (a second UART or screen).
>
> Does this mean that there is only one UART to control the TMC, and not available for a display? (having either the display or the TMC software control, not both at the same time)

From what I can see there are two. One used for the motor control chip and one used to program the device initially. I think you can repurpose that USB one, but you wouldn’t have serial output available then.

I am still experimenting. I really want to buy a whole bunch of these boards, but that extra uart is critical to me.

Tigger777, 2023-12-31:
The ESP32 doesn't have enough pins left for a screen on this board.  However you can add a gcode based screen that uses the serial port connected to the USB chip.   you can connect to the rx&tx lines on the motor uart header.  I the 4 pins closest to the ESP32 to power and communication.  I needed to add a 470r-1k resistor between esp RX and the screen TX.  This is quite an undertaking.  You need to rebuild marlin with all the reporting functions enabled.  Here's my one.  https://www.printables.com/model/323438-pendant-case-for-wt32-sc01, it served my purposes at the time.
I no longer use the E4 boards as I run klipper on my machines now. Actually I haven't used them since I got my Bambu X1C :)

OriginaldCrypt, 2023-12-31:
> you can add a gcode based screen that uses the serial port connected to the USB chip. you can connect to the rx&tx lines on the motor uart header.

These two statements are contradictory, aren't they?
Do you have a drawing/sketch to clarify the design?

Thanks

Tigger777, 2023-12-31:
Ok let me clarify, the below the esp(if the antenna is the top) is labeled i2c on the one side and tx rx 5v g.  The centre row is is connected to all the tmc's the jumpers should be on the i2c side which is actually usart1 on the esp.  The other side is connected to usart0 and the usb chip via 1k series resistors. Sent from my phone On 31 Dec 2023, at 6:01 pm, OriginaldCrypt ***@***.***> wrote:

you can add a gcode based screen that uses the serial port connected to the USB chip. you can connect to the rx&tx lines on the motor uart header.

These two statements are contradictory, aren't they?
Do you have a drawing/sketch to clarify the design?
Thanks

—Reply to this email directly, view it on GitHub, or unsubscribe.You are receiving this because you commented.Message ID: ***@***.***>

OriginaldCrypt, 2023-12-31:
Ok, I am afraid I don't really understood, but I got the point that TWO uart are present (not necesarilly available): one for the TMCs and the other one for the USB port.

So, if I am not mistaken, we can make use of the USB to connect a what you call "GCODE based screen" but immediately after you say that it has to be connected to the "motor UART header".

Which is an example of such as "GCODE based screen"? WT32-SC01 ?
Which are the "motor UART header" pins? Won't it disable the motor UART control?

Thanks for your help!

Tigger777, 2023-12-31:
I called it the motor uart header because it allows you to jumper either usart0 or 1 to the tmc drivers. Yes your understanding is correct, the wtsc01 just overrides the usb chip signals and talks the controller like you would from a gcode  terminal. You could use any of the cheaper displays that are available now.Sent from my phone On 31 Dec 2023, at 9:39 pm, OriginaldCrypt ***@***.***> wrote:
Ok, I am afraid I don't really understood, but I got the point that TWO uart are present (not necesarilly available): one for the TMCs and the other one for the USB port.
So, if I am not mistaken, we can make use of the USB to connect a what you call "GCODE based screen" but immediately after you say that it has to be connected to the "motor UART header".
Which is an example of such as "GCODE based screen"? WT32-SC01 ?
Which are the "motor UART header" pins? Won't it disable the motor UART control?
Thanks for your help!

—Reply to this email directly, view it on GitHub, or unsubscribe.You are receiving this because you commented.Message ID: ***@***.***>

Tigger777, 2024-02-04:
Sorry for the long delay in replying.  Here's the piece of the SCH file,
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
and here's the PCB header P17-P18-P13 from left to right.
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

The jumpers are installed between P17 & P18. P13 is the TTL RS323 lines from the USB to serial chip.  there are 1k series resistors from the usb chip so you can assert signals on P13 to comm directly to the ESP chip and override the CH340's signals.

Tigger777, 2024-02-04:
Here's my board:
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

OriginaldCrypt, 2024-02-05:
It looks like the perfect workaround, do you have a direct link to purchase your exact model?

TextileTopher, 2024-02-05:
> Here's my board: ![image](https://private-user-images.githubusercontent.com/16628902/302092765-d19ca953-4763-4688-b0d7-e92074544ea5.png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)

Tiger - this is awesome. :-)

Tigger777, 2024-02-06:
No sorry I bought these boards Jan 2020, I had quick look on Aliexpress and they're all still v1.0 boards.  There isn't much you can change on these as there no more pins.  One change could be to use GPIO0 as the servo signal to drive a CR/BL touch which is what that green wire is on mine.  I'm happy to share the code for my screen, it's not the most elegant but it worked for me.  You will need to enable all the auto reporting functions in Marlin (temp, position, job progress).

OriginaldCrypt, 2024-12-06:
Hi all, I managed to get this working (at least, I managed to use a conection). I managed to do that after breaking a CYD and hours of testing, but finally it seems to be working.

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

I use FluidNC (https://github.com/bdring/FluidNC) with FluidDial pendant (https://github.com/bdring/FluidDial). The pendant is built on a rotary enconder attached to a CYD (cheap yellow display) acting as remote controller (http://wiki.fluidnc.com/en/hardware/official/CYD_Dial_Pendant and M5 alterrnative http://wiki.fluidnc.com/en/hardware/official/M5Dial_Pendant).
FluidNC, for those who don't know, works like a Klipper firmware for 3d printers: a common firmware for the device and a configuration file, no need to recompile the software after a configuration change.

The Fysetc documentation is very bad. The documentation is incomplete. The electronic diagrams are incomplete. The pin references and pinouts are incomple/not named as in the diagrams. So, try and error. Some facts:

- Pins TX/RX on the right column (named P13 in the electronic diagrams) correspond to TX0/RX0 (as written in the back of the board). TX0 = GPIO1, RX0 = GPIO3. Those seems to be shared with the USB converter, but we can use them by referencing those GPIOs.
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

the FluidNC configuration file excerpt for the UART is:

```
[...]
uart2:
  txd_pin: gpio.1
  rxd_pin: gpio.3
  rts_pin: NO_PIN
  cts_pin: NO_PIN
  baud: 1000000
  mode: 8N1

uart_channel2:
  report_interval_ms: 75
  uart_num: 2
[...]
```

- I will test more later , but it looks like the UART0 can be used along with UART1 (motor UART) but not with USB.

BR

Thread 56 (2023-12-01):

TMC2209 UART driver error

yoroboticscolombia, 2023-12-01:
Hi, Im trying to configure the board and change the driver current, but i tried setting monitor driver status, but i get this message:

18:58:52.344 : E (5870) uart: uart_get_buffered_data_len(1342): uart driver error
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

what can be causing this.
I have already knowledge of marlin and esp3d.

thanks.

tizbac, 2024-03-30:
Same issue here, did you solve it somehow?

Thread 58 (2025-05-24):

error: 'unsigned char String::concat(const char*, unsigned int)' is protected

suliaman99, 2025-05-24:
While compiling, and after it finishes making the object file, I get the error
C:\Users\user\.platformio\packages\framework-arduinoespressif32@3.10004.210126\cores\esp32/WString.h: In function 'String generateEventMessage(const char*, const char*, uint32_t, uint32_t)':
C:\Users\user\.platformio\packages\framework-arduinoespressif32@3.10004.210126\cores\esp32/WString.h:288:23: error: 'unsigned char String::concat(const char*, unsigned int)' is protected
         unsigned char concat(const char *cstr, unsigned int length);
                       ^
.pio\libdeps\fysetc_e4\ESPAsyncWebServer\src\AsyncEventSource.cpp:99:46: error: within this context
     str.concat(lineStart, lineEnd - lineStart);
                                              ^
and so on, I think it's because of the platformIO, but I couldn't find an old version on the extension

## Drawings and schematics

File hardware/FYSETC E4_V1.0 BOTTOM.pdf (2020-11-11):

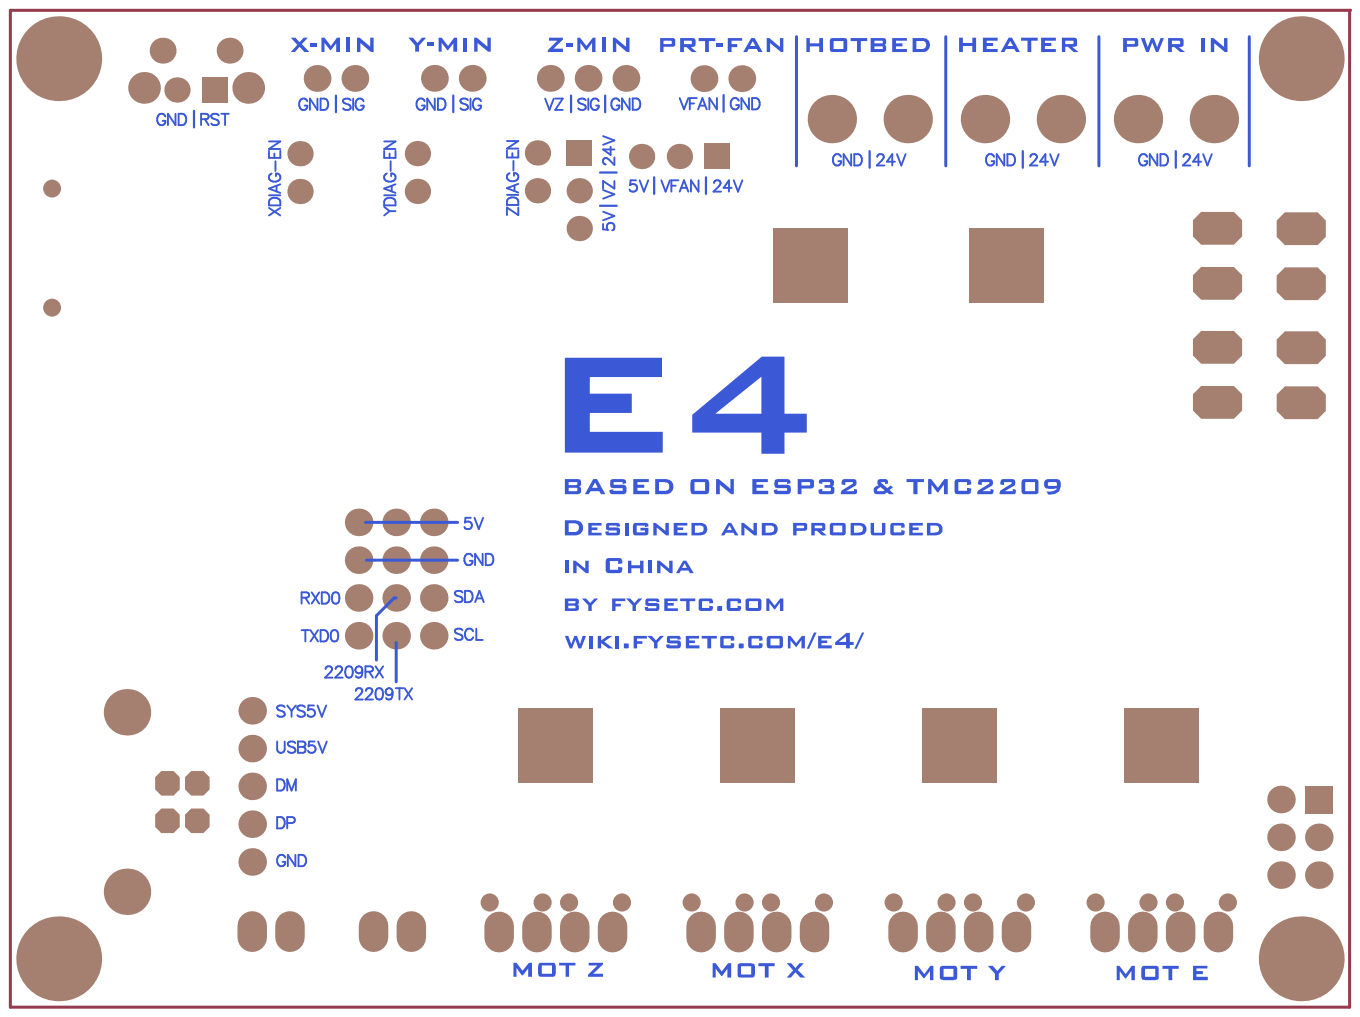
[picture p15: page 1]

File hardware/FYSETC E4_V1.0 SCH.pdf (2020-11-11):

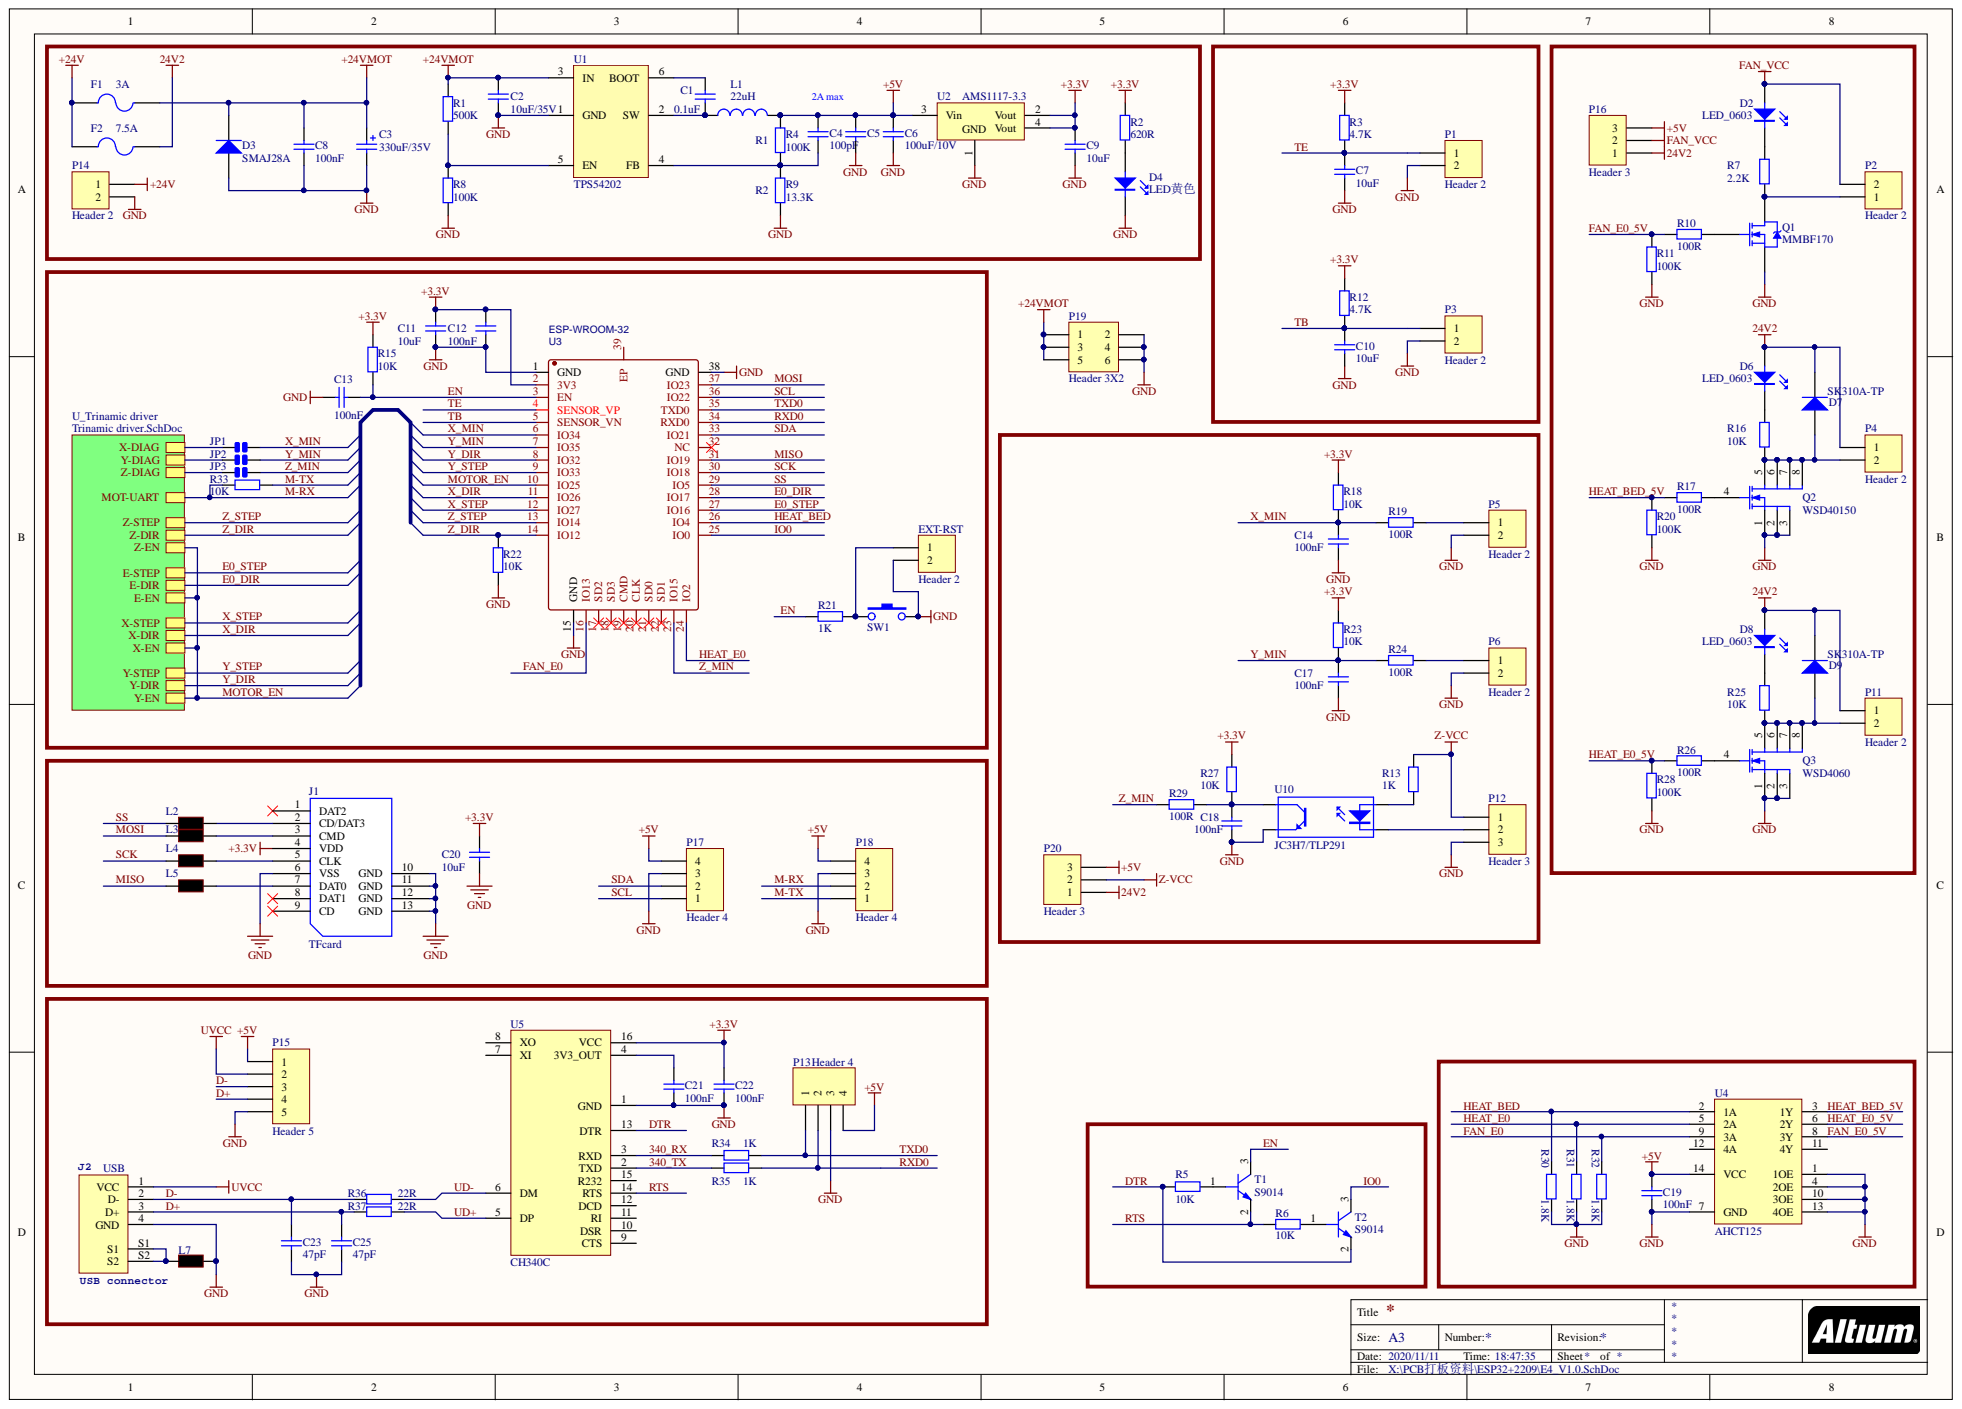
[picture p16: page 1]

* Title | * * * * *

Size: A3 | Number: * | Revision: *
Date: 2020/11/11 Time: 18:47:35 | | Sheet * of *

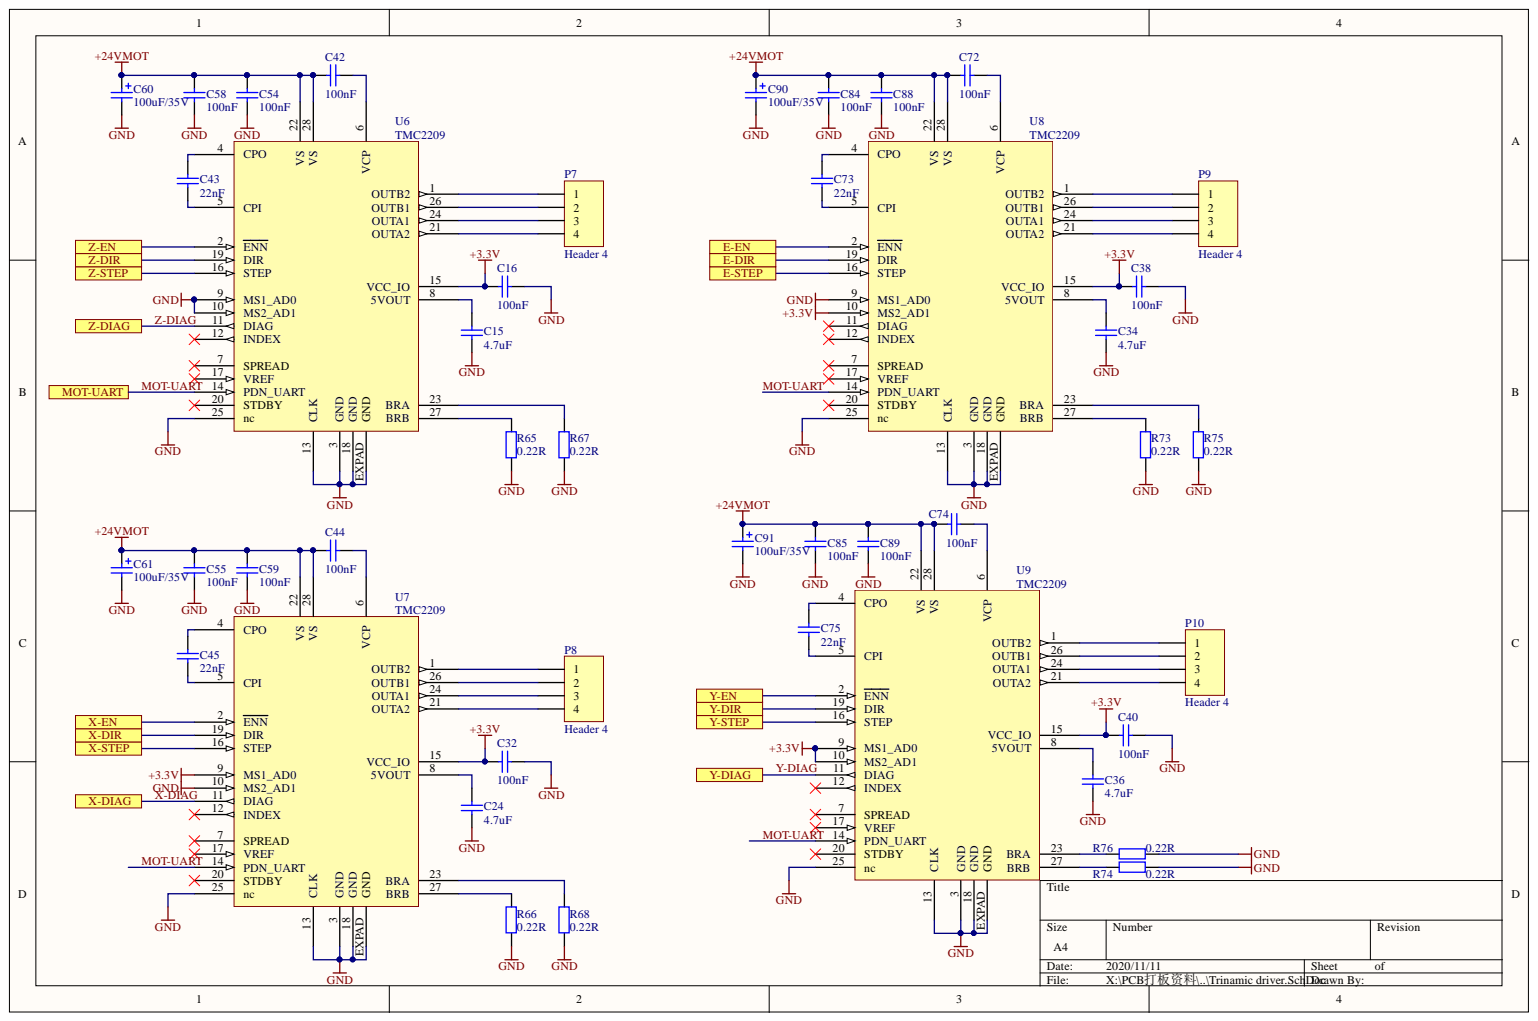
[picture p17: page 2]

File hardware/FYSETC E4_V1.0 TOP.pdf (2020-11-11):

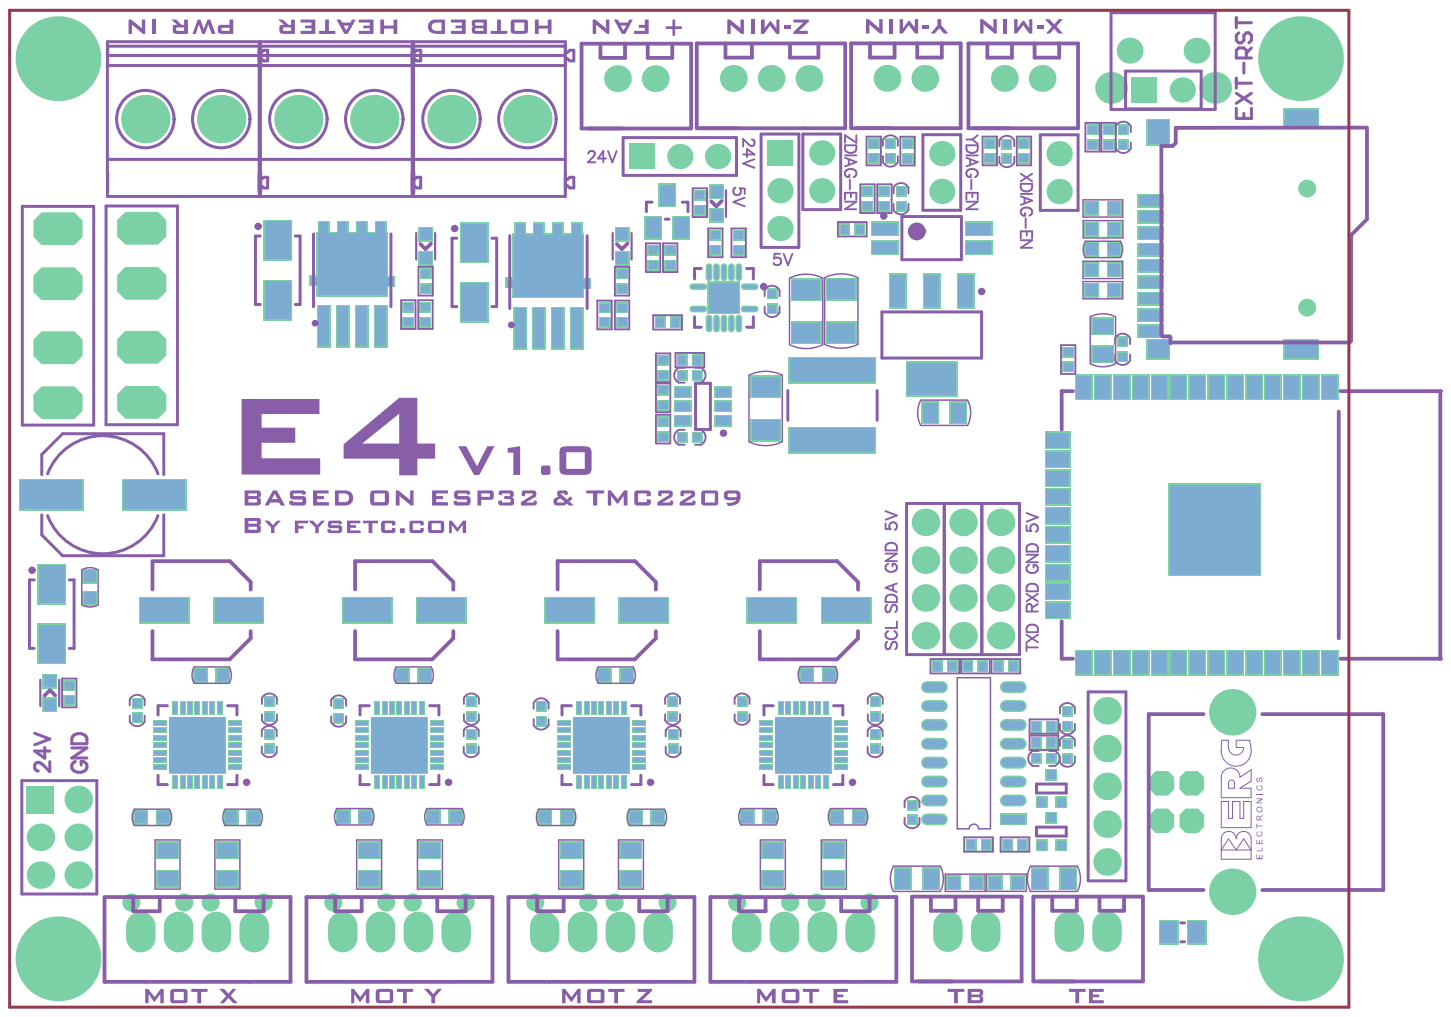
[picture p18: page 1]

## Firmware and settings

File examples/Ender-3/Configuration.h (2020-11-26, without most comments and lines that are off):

#pragma once
#define CONFIGURATION_H_VERSION 020006
#define STRING_CONFIG_H_AUTHOR "(none, default config)" // Who made the changes.
#define SHOW_BOOTSCREEN
#define SERIAL_PORT 0
#define BAUDRATE 115200
  #define MOTHERBOARD BOARD_FYSETC_E4
#define EXTRUDERS 1
#define DEFAULT_NOMINAL_FILAMENT_DIA 1.75
#define TEMP_SENSOR_0 1
#define TEMP_SENSOR_1 0
#define TEMP_SENSOR_2 0
#define TEMP_SENSOR_3 0
#define TEMP_SENSOR_4 0
#define TEMP_SENSOR_5 0
#define TEMP_SENSOR_6 0
#define TEMP_SENSOR_7 0
#define TEMP_SENSOR_BED 1
#define TEMP_SENSOR_PROBE 0
#define TEMP_SENSOR_CHAMBER 0
#define DUMMY_THERMISTOR_998_VALUE 25
#define DUMMY_THERMISTOR_999_VALUE 100
#define MAX_REDUNDANT_TEMP_SENSOR_DIFF 10
#define TEMP_RESIDENCY_TIME     10  // (seconds) Time to wait for hotend to "settle" in M109
#define TEMP_WINDOW              1  // (°C) Temperature proximity for the "temperature reached" timer
#define TEMP_HYSTERESIS         10  // (°C) Temperature proximity considered "close enough" to the target
#define TEMP_BED_RESIDENCY_TIME 10  // (seconds) Time to wait for bed to "settle" in M190
#define TEMP_BED_WINDOW          1  // (°C) Temperature proximity for the "temperature reached" timer
#define TEMP_BED_HYSTERESIS      3  // (°C) Temperature proximity considered "close enough" to the target
#define HEATER_0_MINTEMP   5
#define HEATER_1_MINTEMP   5
#define HEATER_2_MINTEMP   5
#define HEATER_3_MINTEMP   5
#define HEATER_4_MINTEMP   5
#define HEATER_5_MINTEMP   5
#define HEATER_6_MINTEMP   5
#define HEATER_7_MINTEMP   5
#define BED_MINTEMP        5
#define HEATER_0_MAXTEMP 275
#define HEATER_1_MAXTEMP 275
#define HEATER_2_MAXTEMP 275
#define HEATER_3_MAXTEMP 275
#define HEATER_4_MAXTEMP 275
#define HEATER_5_MAXTEMP 275
#define HEATER_6_MAXTEMP 275
#define HEATER_7_MAXTEMP 275
#define BED_MAXTEMP      150
#define PIDTEMP
#define BANG_MAX 255     // Limits current to nozzle while in bang-bang mode; 255=full current
#define PID_MAX BANG_MAX // Limits current to nozzle while PID is active (see PID_FUNCTIONAL_RANGE below); 255=full current
#define PID_K1 0.95      // Smoothing factor within any PID loop
  #define DEFAULT_Kp 22.2
  #define DEFAULT_Ki 1.08
  #define DEFAULT_Kd 114
#define MAX_BED_POWER 255 // limits duty cycle to bed; 255=full current
  #define PID_FUNCTIONAL_RANGE 10 // If the temperature difference between the target temperature and the actual temperature
#define EXTRUDE_MINTEMP 170
#define PREVENT_LENGTHY_EXTRUDE
#define EXTRUDE_MAXLENGTH 200
#define THERMAL_PROTECTION_HOTENDS // Enable thermal protection for all extruders
#define THERMAL_PROTECTION_BED     // Enable thermal protection for the heated bed
#define THERMAL_PROTECTION_CHAMBER // Enable thermal protection for the heated chamber
#define USE_XMIN_PLUG
#define USE_YMIN_PLUG
#define USE_ZMIN_PLUG
#define ENDSTOPPULLUPS
#define X_MIN_ENDSTOP_INVERTING false // Set to true to invert the logic of the endstop.
#define Y_MIN_ENDSTOP_INVERTING false // Set to true to invert the logic of the endstop.
#define Z_MIN_ENDSTOP_INVERTING false // Set to true to invert the logic of the endstop.
#define X_MAX_ENDSTOP_INVERTING false // Set to true to invert the logic of the endstop.
#define Y_MAX_ENDSTOP_INVERTING false // Set to true to invert the logic of the endstop.
#define Z_MAX_ENDSTOP_INVERTING false // Set to true to invert the logic of the endstop.
#define Z_MIN_PROBE_ENDSTOP_INVERTING false // Set to true to invert the logic of the probe.
#define X_DRIVER_TYPE  TMC2209
#define Y_DRIVER_TYPE  TMC2209
#define Z_DRIVER_TYPE  TMC2209
#define E0_DRIVER_TYPE TMC2209
#define DEFAULT_AXIS_STEPS_PER_UNIT   { 80, 80, 400, 93 }
#define DEFAULT_MAX_FEEDRATE          { 300, 300, 5, 25 }
#define DEFAULT_MAX_ACCELERATION      { 3000, 3000, 100, 10000 }
#define DEFAULT_ACCELERATION          2000    // X, Y, Z and E acceleration for printing moves
#define DEFAULT_RETRACT_ACCELERATION  2000    // E acceleration for retracts
#define DEFAULT_TRAVEL_ACCELERATION   2000    // X, Y, Z acceleration for travel (non printing) moves
#define DEFAULT_EJERK    5.0  // May be used by Linear Advance
  #define JUNCTION_DEVIATION_MM 0.013 // (mm) Distance from real junction edge
  #define JD_HANDLE_SMALL_SEGMENTS    // Use curvature estimation instead of just the junction angle
#define Z_MIN_PROBE_USES_Z_MIN_ENDSTOP_PIN
#define NOZZLE_TO_PROBE_OFFSET { 10, 10, 0 }
#define PROBING_MARGIN 10
#define XY_PROBE_SPEED 8000
#define Z_PROBE_SPEED_FAST HOMING_FEEDRATE_Z
#define Z_PROBE_SPEED_SLOW (Z_PROBE_SPEED_FAST / 2)
#define Z_CLEARANCE_DEPLOY_PROBE   10 // Z Clearance for Deploy/Stow
#define Z_CLEARANCE_BETWEEN_PROBES  5 // Z Clearance between probe points
#define Z_CLEARANCE_MULTI_PROBE     5 // Z Clearance between multiple probes
#define Z_PROBE_LOW_POINT          -2 // Farthest distance below the trigger-point to go before stopping
#define Z_PROBE_OFFSET_RANGE_MIN -20
#define Z_PROBE_OFFSET_RANGE_MAX 20
#define X_ENABLE_ON 0
#define Y_ENABLE_ON 0
#define Z_ENABLE_ON 0
#define E_ENABLE_ON 0 // For all extruders
#define DISABLE_X false
#define DISABLE_Y false
#define DISABLE_Z false
#define DISABLE_E false             // For all extruders
#define DISABLE_INACTIVE_EXTRUDER   // Keep only the active extruder enabled
#define INVERT_X_DIR true
#define INVERT_Y_DIR true
#define INVERT_Z_DIR false
#define INVERT_E0_DIR true
#define INVERT_E1_DIR false
#define INVERT_E2_DIR false
#define INVERT_E3_DIR false
#define INVERT_E4_DIR false
#define INVERT_E5_DIR false
#define INVERT_E6_DIR false
#define INVERT_E7_DIR false
#define X_HOME_DIR -1
#define Y_HOME_DIR -1
#define Z_HOME_DIR -1
#define X_BED_SIZE 230
#define Y_BED_SIZE 230
#define X_MIN_POS 0
#define Y_MIN_POS 0
#define Z_MIN_POS 0
#define X_MAX_POS X_BED_SIZE
#define Y_MAX_POS Y_BED_SIZE
#define Z_MAX_POS 260
#define MIN_SOFTWARE_ENDSTOPS
  #define MIN_SOFTWARE_ENDSTOP_X
  #define MIN_SOFTWARE_ENDSTOP_Y
  #define MIN_SOFTWARE_ENDSTOP_Z
#define MAX_SOFTWARE_ENDSTOPS
  #define MAX_SOFTWARE_ENDSTOP_X
  #define MAX_SOFTWARE_ENDSTOP_Y
  #define MAX_SOFTWARE_ENDSTOP_Z
#define HOMING_FEEDRATE_XY (50*60)
#define HOMING_FEEDRATE_Z  (4*60)
#define VALIDATE_HOMING_ENDSTOPS
#define EEPROM_SETTINGS     // Persistent storage with M500 and M501
#define EEPROM_CHITCHAT       // Give feedback on EEPROM commands. Disable to save PROGMEM.
#define EEPROM_BOOT_SILENT    // Keep M503 quiet and only give errors during first load
#define HOST_KEEPALIVE_FEATURE        // Disable this if your host doesn't like keepalive messages
#define DEFAULT_KEEPALIVE_INTERVAL 2  // Number of seconds between "busy" messages. Set with M113.
#define BUSY_WHILE_HEATING            // Some hosts require "busy" messages even during heating
#define PREHEAT_1_LABEL       "PLA"
#define PREHEAT_1_TEMP_HOTEND 180
#define PREHEAT_1_TEMP_BED     70
#define PREHEAT_1_FAN_SPEED     0 // Value from 0 to 255
#define PREHEAT_2_LABEL       "ABS"
#define PREHEAT_2_TEMP_HOTEND 240
#define PREHEAT_2_TEMP_BED    110
#define PREHEAT_2_FAN_SPEED     0 // Value from 0 to 255
#define PRINTJOB_TIMER_AUTOSTART
#define LCD_LANGUAGE en
#define DISPLAY_CHARSET_HD44780 JAPANESE
#define LCD_INFO_SCREEN_STYLE 0
#define SDSUPPORT
#define SPI_SPEED SPI_HALF_SPEED
#define SOFT_PWM_SCALE 0
#define SERVO_DELAY { 300 }

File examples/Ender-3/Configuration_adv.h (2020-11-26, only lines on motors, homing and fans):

#define E0_AUTO_FAN_PIN -1
#define E1_AUTO_FAN_PIN -1
#define E2_AUTO_FAN_PIN -1
#define E3_AUTO_FAN_PIN -1
#define E4_AUTO_FAN_PIN -1
#define E5_AUTO_FAN_PIN -1
#define E6_AUTO_FAN_PIN -1
#define E7_AUTO_FAN_PIN -1
#define CHAMBER_AUTO_FAN_PIN -1
#define HOMING_BUMP_MM      { 5, 5, 2 }       // (mm) Backoff from endstops after first bump
#define HOMING_BUMP_DIVISOR { 2, 2, 4 }       // Re-Bump Speed Divisor (Divides the Homing Feedrate)
#define MICROSTEP_MODES { 16, 16, 16, 16, 16, 16 } // [1,2,4,8,16]
    #define X_CURRENT       650        // (mA) RMS current. Multiply by 1.414 for peak current.
    #define X_CURRENT_HOME  X_CURRENT  // (mA) RMS current for sensorless homing
    #define X_MICROSTEPS     16    // 0..256
    #define Y_CURRENT       650
    #define Y_CURRENT_HOME  Y_CURRENT
    #define Y_MICROSTEPS     16
    #define Z_CURRENT       800
    #define Z_CURRENT_HOME  Z_CURRENT
    #define Z_MICROSTEPS     16
    #define E0_CURRENT      600
    #define E0_MICROSTEPS    16
  #define X_HYBRID_THRESHOLD     100  // [mm/s]
  #define X2_HYBRID_THRESHOLD    100
  #define Y_HYBRID_THRESHOLD     100
  #define Y2_HYBRID_THRESHOLD    100
  #define Z_HYBRID_THRESHOLD       3
  #define Z2_HYBRID_THRESHOLD      3
  #define Z3_HYBRID_THRESHOLD      3
  #define Z4_HYBRID_THRESHOLD      3
  #define E0_HYBRID_THRESHOLD     30
  #define E1_HYBRID_THRESHOLD     30
  #define E2_HYBRID_THRESHOLD     30
  #define E3_HYBRID_THRESHOLD     30
  #define E4_HYBRID_THRESHOLD     30
  #define E5_HYBRID_THRESHOLD     30
  #define E6_HYBRID_THRESHOLD     30
  #define E7_HYBRID_THRESHOLD     30

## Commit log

2020-11-05 Upload firmware
    [Configuration.h, Configuration_adv.h]
2020-11-07 Add ESPLib features file
    [ESPLib-features.xls]
2020-11-26 Add Ender-3 example
    [Case.STL, Configuration.h, Configuration_adv.h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]
2020-12-04 Update ESPLib features file
    [ESPLib-features.xls]
2022-03-24 Update 3D
    3D models for ESP32, fuseholder, and CH340 inserted into Altium footprints. 3D model export updated with mounting holes, 3D black colors.
2022-07-29 Add pin definition
2023-12-21 Add Marlin 2.1.x compile infos

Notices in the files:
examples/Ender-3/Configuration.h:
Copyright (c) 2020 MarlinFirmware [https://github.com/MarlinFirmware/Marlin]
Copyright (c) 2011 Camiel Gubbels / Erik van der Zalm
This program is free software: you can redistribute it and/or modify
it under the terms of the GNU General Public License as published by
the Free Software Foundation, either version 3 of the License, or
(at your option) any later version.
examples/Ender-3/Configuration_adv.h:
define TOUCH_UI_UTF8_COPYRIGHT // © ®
